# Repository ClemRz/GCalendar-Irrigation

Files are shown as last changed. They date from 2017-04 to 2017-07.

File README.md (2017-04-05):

# Google Calendar Irrigation system

**How to use it?** Add a task to your Google Calendar and the irrigation of your garden/lawn will start when the event begins and stop when it ends!

**Why I invented that?** I don't like the interface of cheap irrigation programmers, the irrigation parameters are not flexible enough and it can't be controlled remotely. I wanted a cheap wifi irrigation programmer but I didn't want to build the entire UI for the ESP8266, I preferred to be able to change the irrigation planning from anywhere with simple means. I decided to have the ESP polling one of my Google Calendars, with events to turn on and off the valve at the correct timing.

**How is this made possible?** A ESP8266 connects to your Google Calendar via your home Wifi (using a Google Script) and commands a solenoid valve.

## TOC

  - [Hardware design](#hardware-design)
  - [Software design](#software-design)

## Hardware design

Parts list:

  - 3 x Capacitors (22µF, 0.1µF, 4700µF)
  - 1 x DC motor driver (DRV8872 in this case)
  - 1 x ESP8266 (version ESP07)
  - 1 x 3.3V Voltage regulator (LT1529-3.3 for instance)
  - 1 x 12V 1.5A charger
  - 1 x Female plug (same size as the charger's plug)
  - 1 x Prototyping board
  - 1 x Latching solenoid valve (scavenged from an Orbit 58874N)
  - 3 x Momentary push buttons
  - 1 x Rocker switch
  - 3 x Straight male headers
  - Some wires

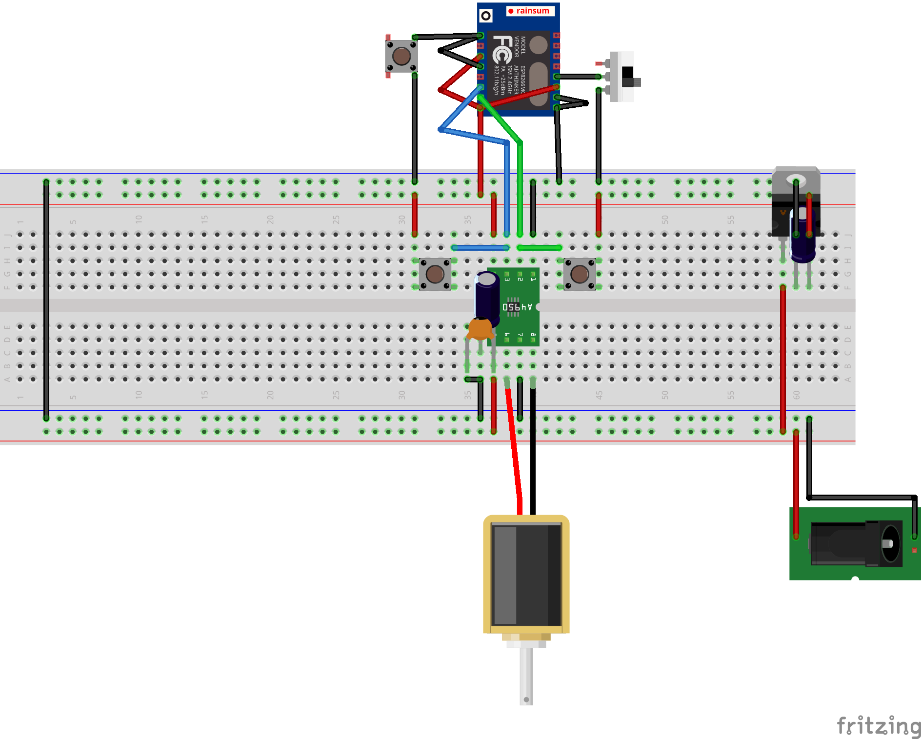
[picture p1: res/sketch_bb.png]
Sketch


## Software design

### Google Script parameters

  - `_calendarName`: the calendar name that is going to be taken into account
  - `_checkInRate`: the polling rate

### ESP8266 Code

#### Dependencies 

  - [ArduinoJson library](https://github.com/bblanchon/ArduinoJson)
  - [HTTPS Redirect library](https://github.com/electronicsguy/ESP8266/tree/master/HTTPSRedirect)

#### Parameters

Change the constants according to your needs:

  - `DEFAULT_WAKEUP_RATE`: how long should the device be sleeping between each polling. This is the default value which will be overriden at the first call to the Google Script
  - `SSID`: your wifi's SSID
  - `PASSWORD`: your wifi's password
  - `SCRIPT_ID`: your Google Script ID (can be found in the deploy url)
  - `DEBUG`: turn to 1 if you want to see debug information in the console log
  - `CLOSE`: ESP pin number that is connected to the _close_ input of the driver
  - `OPEN`: ESP pin number that is connected to the _open_ input of the driver

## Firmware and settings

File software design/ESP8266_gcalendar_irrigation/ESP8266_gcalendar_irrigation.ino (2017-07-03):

/*
    Copyright (C) 2017 Clément Ronzon

    This file is part of GCalendarIrrigation.

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
    You should have received a copy of the GNU General Public License
    along with GCalendarIrrigation.  If not, see <http://www.gnu.org/licenses/>.
 */

#include <ESP8266WiFi.h>
#include "HTTPSRedirect.h"
#include <ArduinoJson.h>

#define MICROSEC              1000000L
#define MILLISEC              1000L
#define SEC                   1L
#define MINUTE                (unsigned int) 60L*SEC
#define HOUR                  (unsigned int) 60L*MINUTE
#define DAY                   (unsigned long) 24L*HOUR

/* 
 * ======================================
 *      User defined constants
 * ======================================
*/
#define DEFAULT_POLLING_RATE  5*MINUTE
#define SSID                  "YOUR_SSID"
#define PASSWORD              "YOUR_PASSWORD"
#define SCRIPT_ID             "YOUR_GOOGLE_SCRIPT_ID"
#define DEBUG                 1
// ======================================

// Pins allocation
#define N_FAULT               4
#define CLOSE                 12
#define OPEN                  13

// HTTPS parameters
#define HTTPS_PORT            443
#define HOST                  "script.google.com"
#define URL                   "https://" HOST "/macros/s/" SCRIPT_ID "/exec"
#define SUCCESS               "\"status\":\"success\""
#define MAX_WIFI_ATTEMPTS     60
#define MAX_HTTPS_ATTEMPTS    5
#define HTTPS_REINTENT_DELAY  2*SEC

// Deep-sleep time limit
#define MAX_SLEEP_TIME        71L*MINUTE

// Global variables
HTTPSRedirect* client = NULL;
long _pollingRate = DEFAULT_POLLING_RATE;
int _attempts = 0;

void setup() {
#if DEBUG
  initSerial();
#endif
  initIO();
  initWiFi();
}

void loop() {
  if (_attempts <= MAX_WIFI_ATTEMPTS) {
    _attempts = 0;
    String response = httpsGet();
    if (response != "") {
      process(response);
    } else closeValve();
  } else closeValve();
  sleep();
}

void process(String response) {
  StaticJsonBuffer<200> jsonBuffer;
  JsonObject& root = jsonBuffer.parseObject(response);
  if (root.success()) {
    String status = root["status"];
    if (status == "success") {
      _pollingRate = root["data"]["nextCheckIn"];
      if (_pollingRate > MAX_SLEEP_TIME) _pollingRate = MAX_SLEEP_TIME;
      if (root["data"]["openValve"]) openValve();
      if (root["data"]["closeValve"]) closeValve();
    } else {
#if DEBUG
      Serial.print(F("Unsuccessful response: ")); Serial.println(status);
#endif
      closeValve();
    }
  } else {
#if DEBUG
    Serial.println(F("Failed to parse JSON"));
#endif
    closeValve();
  }
}

void sleep() {
#if DEBUG
  Serial.print(F("Go to sleep for "));
  Serial.print(_pollingRate);
  Serial.println(F("s."));
#endif  //DEBUG
  if (_pollingRate == 0) _pollingRate = 1;
  ESP.deepSleep(_pollingRate * MICROSEC);
}

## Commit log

2017-04-05 Adds hardware design
    [sketch.fzz]
2017-04-05 Updates sketch
    [sketch.fzz]

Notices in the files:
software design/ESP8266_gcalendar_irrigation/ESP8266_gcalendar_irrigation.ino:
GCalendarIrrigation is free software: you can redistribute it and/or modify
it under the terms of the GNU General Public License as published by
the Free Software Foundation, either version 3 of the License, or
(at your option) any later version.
